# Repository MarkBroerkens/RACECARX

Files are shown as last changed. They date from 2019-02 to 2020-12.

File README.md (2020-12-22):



# RACECAR/X

1:10 autonomous RC robocar that is controlled by NVIDIA AGX Xavier.
Please find furher documentation on the [RACECARX website](https://markbroerkens.github.io/RACECARX/docs/)

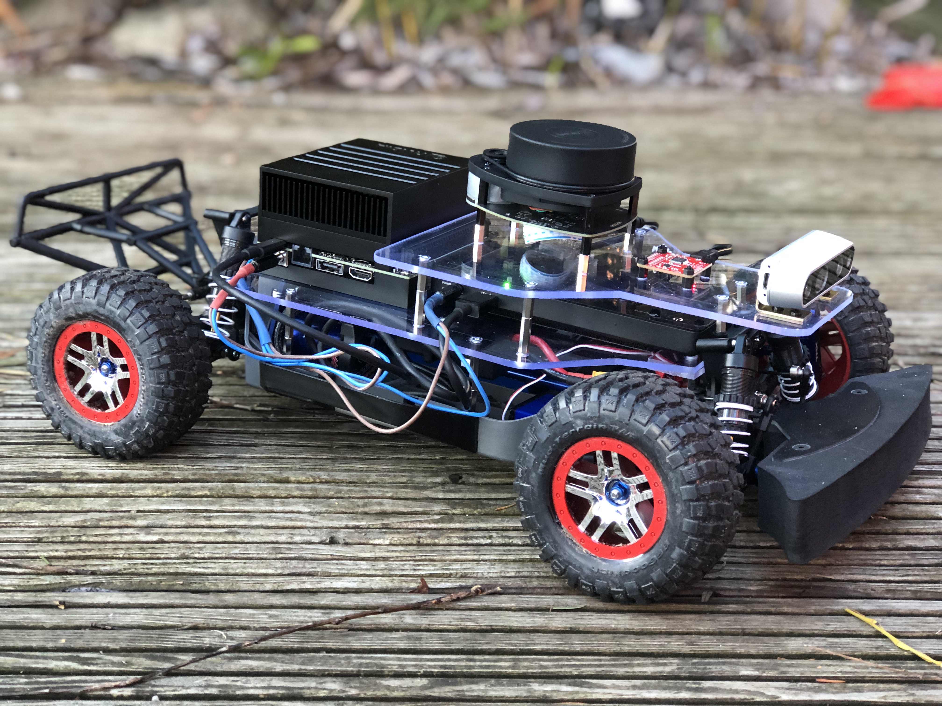
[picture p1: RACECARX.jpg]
RACECAR/X


## Capabilities
* Teleoperation
* Autonomous navigation

## Used technologies
* Docker
* ROS Melodic
* NVidia Xavier
* VESC speed controller
* Intel realsense d435i depth camera
* RPLidar A1 2D laser scanner
* IMU

## Structure of this repository

* [docs](docs) source of the website [RACECARX website](https://markbroerkens.github.io/RACECARX/).
* [hardware](hardware) hardware related resources such as laser cutter descriptions of the platforms
* [software](software) scripts for setting up the software on the Nvidia Jetson and on the PC host 

## Contribution Guide
You are very welcome to contribute to the project. E.g. by 

* reporting an issue via the [github issue](https://github.com/MarkBroerkens/RACECARX/issues) tracker 
* creating a [pull](https://github.com/MarkBroerkens/RACECARX/pulls) request. 

The [Udacity Git Commit Message Style Guide](http://udacity.github.io/git-styleguide/) apply.

The [github workflow](.github/workflows/deploy_website.yml) automatically builds and deploys the website into the [gh-pages](https://github.com/MarkBroerkens/RACECARX/tree/gh-pages) branch. 

You can build the site locally: `bundle exec jekyll build -s docs -d _site`.

## License
The content of this repository is licensed under a [MIT](LICENSE) License

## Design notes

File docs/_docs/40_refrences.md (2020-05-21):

---
permalink: /docs/references/
title: "References"
sidebar:
  nav: "docs"
---

## Similar Projects
RACECAR/X is inspired by the following projects. 

* [MIT RACECAR](https://mit-racecar.github.io/) - MIT RACECAR is an open-source powerful platform for robotics research and education.
* [Jetson racecar](https://www.jetsonhacks.com/category/robotics/jetson-racecar/)
* [F1/10 Autonomous Racing Competition](http://f1tenth.org/) - international community of researchers, engineers, and autonomous systems enthusiasts. It was originally founded at the University of Pennsylvania in 2016 but has since spread to many other institutions worldwide. Great [build](https://f1tenth.org/build.html) instructions and [lectures](https://f1tenth.org/learn.html).
* [OpenZeka Marc](https://github.com/openzeka/marc) - ([translated to english](http://translate.google.com/translate?hl=&sl=tr&tl=en&u=https%3A%2F%2Fopenzeka.com%2Fmarc%2F&sandbox=1))
* [Hypha-ROS racecar](https://hypharosworkshop.wordpress.com/) - Low-cost, high speed (600USD, 3 m/s) 1/10 Autonomous ROS RaceCar (with tutorial for beginner)
* [eagleMK4](https://github.com/r7vme/eagleMK4) - The prototype of autonomous RC car based on MIT Racecar platform
* [Project Omicron](https://project-omicron.github.io/index.html) - build a robot for the Robocup@Work competition
* [JetRacer](https://github.com/NVIDIA-AI-IOT/jetracer) - an autonomous AI racecar using NVIDIA Jetson Nano
* [Multi-agent System for non-Holonomic Racing (MuSHR)](https://mushr.io/) - an open-source robotic hardware and software platform for learning and researching AI in a the setting of autonomous vehicles and mobile robotics.

## Related to Nvidia Jetson

* [Jetson Nano Tools](https://github.com/karaage0703/jetson-nano-tools) - Jetson Nano useful tools (setup, examples)
* [Jetcard install](https://github.com/NVIDIA-AI-IOT/jetcard/blob/master/install.sh) - install script of nvidia jetcard
* [NVIDIA AI IOT](https://github.com/NVIDIA-AI-IOT) - NVIDIA AI IOT Github repositories
* [Isaac SDK](https://docs.nvidia.com/isaac/isaac/doc/index.html) - the main software toolkit for NVIDIA robotics
* [Jetson Community Projects](https://developer.nvidia.com/embedded/community/jetson-projects)
* [Jetson Zoo](https://elinux.org/Jetson_Zoo) - contains instructions for installing various open source add-on packages and frameworks on NVIDIA Jetson, in addition to a collection of DNN models for inferencing.

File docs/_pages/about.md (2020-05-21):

---
permalink: /about/
title: "About"
author_profile: true
---

This project is higly inspired by the [MIT racecar](https://mit-racecar.github.io/) and [Jetson racecar](https://www.jetsonhacks.com/category/robotics/jetson-racecar/).

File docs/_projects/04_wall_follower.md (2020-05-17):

---
permalink: /projects/wall_follower
title: "Wall Follower"
excerpt: Wall follower based on lidar data.
toc: false
classes: wide
---

{% include video id="c6wClUE2E_Q" provider="youtube" %}

{% include video id="4Rs8uSq79dI" provider="youtube" %}

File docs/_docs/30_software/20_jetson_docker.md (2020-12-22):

---
permalink: /docs/software/jetson_docker
title: "Software Setup - Docker on Jetson Xavier"
toc: true
---

The docker images are created on top of the l4t-base image from the Nvidia GPU Cloud.

## Get the installation scripts

```bash
echo 'export RACECARX=$HOME/racecarx' >> ~/.bashrc
echo 'export RACECARX_JETSON=$RACECARX/git/RACECARX/software/jetson' >> ~/.bashrc
source ~/.bashrc
```

```bash
mkdir -p $RACECARX/git
cd $RACECARX/git
git clone https://github.com/MarkBroerkens/RACECARX.git
```

## Install Udev Rules for the Peripherals 
(TODO: should go to pheripherals)

* Alias the Sparkfun 9DoF as /dev/imu
* Alias for electronic speed controller as /dev/vesc
* Alias for the rplidar as /dev/rplidar
* ALias for Intel RealSense D435i camera

```bash
cd $RACECARX_JETSON
./scripts/jetsonInstallUdev.sh
```

make sure we have write access to the VESC and IMU devices

```bash
sudo adduser $USER dialout
```

Further references:

* [ROS and Udev Rules](https://www.clearpathrobotics.com/assets/guides/kinetic/ros/Udev%20Rules.html)

## Build docker container
```bash
cd $RACECARX_JETSON
./scripts/docker_build_ros.sh
```

The docker image supports the following features:

1. Nvidia base image: l4t-base (r32.4.3)
2. ROS melodic
3. Realsense camera

## Initial setup
```bash
cd $RACECARX_JETSON
./scripts/docker_build_racecarx.sh
```

# Run the docker container in interactive mode

```bash
cd $RACECARX_JETSON
./scripts/docker_run_racecarx.sh
```

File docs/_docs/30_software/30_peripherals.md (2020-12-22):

---
permalink: /docs/software/peripherals
title: "Software Setup - Sensors and Actuators"
toc: true
---

## Controller Sony DualShock 4 V2
Connect the Controller via bluetooth

```bash
sudo bluetoothctl
```
Enable the agent and set it as default:

```bash
[bluetooth]# agent on
[bluetooth]# default-agent
```

Power on the Bluetooth controller, and set it as discoverable and pairable:

```bash
[bluetooth]# power on
[bluetooth]# discoverable on
[bluetooth]# pairable on
```

Scan for devices:

```bash
[bluetooth]# scan on
```

Put the DualShock 4 into pairing mode by pressing and holding the PlayStation and Share buttons until the light bar starts flashing.

Discover the DualShock 4 MAC address:

```bash
[bluetooth]# devices
```

Pair with the DualShock 4:

```bash
[bluetooth]# pair DC:0C:FF:B2:79:EE
```

Allow the service authorization request:

```bash
[agent]Authorize service service_uuid (yes/no): yes
```

Trust the DualShock 4:

```bash
[bluetooth]# trust DC:0C:FF:B2:79:EE
```

The DualShock 4 is now paired.

Turn the DualShock 4 off when it's no longer in use by pressing and holding the PlayStation button for 10 seconds. Press the PlayStation button to use the DualShock 4 again.

Test the controller

```bash
sudo apt-get install joystick
ls /dev/input 
jstest /dev/input/js0
```

## Realsense d435i camera
Run the racecarx docker container in interactive mode

```bash
~/racecarx/RACECARX/racecarx.sh
```

Run the firmware update tool and print the connected devices

```bash
rs-fw-update -l
```

My oputput looks like this

```
connected devices:
1) Name: Intel RealSense D435I, serial number: xxxxxxxxx, update serial number: xxxxxxxx, firmware version: 05.11.06.250, USB type: 3.2
```

Find the latest firmware and copy its link 
[latest firmware](https://downloadcenter.intel.com/download/29255/Latest-Firmware-for-Intel-RealSense-D400-Product-Family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)

download and install latest firmware. See also [here](https://dev.intelrealsense.com/docs/firmware-update-tool)

```bash
cd /tmp
wget https://downloadmirror.intel.com/29703/eng/D400_Series_Development_FW_5_12_6_0.zip
apt update # gets the index
apt-get install unzip # installs unzip
unzip D400_Series_Development_FW_5_12_6_0.zip
rs-fw-update -f Signed_Image_UVC_5_12_6_0.bin
```

we should see the updated firmware version

```bash
rs-fw-update -l
```

After the update my output looks like this:
```
connected devices:
1) Name: Intel RealSense D435I, serial number: xxxxxxxxx, update serial number: xxxxxxxx, firmware version: 05.12.06.00, USB type: 3.2
```

## Focbox Electronic Speed Control
* Get the [VESC Tool](https://vesc-project.com/vesc_tool). The free version is sufficient. 
* The required Firmware [VESC_servoout.bin](https://github.com/vedderb/vesc_tool/blob/master/res/firmwares/410_o_411_o_412/VESC_servoout.bin) is available in the [vedderb/vesc_tool](https://github.com/vedderb/vesc_tool) github repository at [res/firmwares/410_o_411_o_412](https://github.com/vedderb/vesc_tool/blob/master/res/firmwares/410_o_411_o_412/)

## SparkFun 9DoF Razor IMU M0
Install Arduino Firmware as described [here](https://github.com/MarkBroerkens/razor_imu_9dof)

## RPLidar A1M8
Installation consists of proper configuration of UDEV rules.

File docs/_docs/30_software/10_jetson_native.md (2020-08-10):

---
permalink: /docs/software/jetson_native
title: "Software Setup - Jetson Xavier"
toc: true
---

## Install JetPack 4.4
* Download and install [NVIDIA SDK Manager](https://developer.nvidia.com/embedded/jetpack)
* Note: Select the manual installation mode. 
  Automatic mode might have issues when starting up in headless mode. See bug 200525134 in the [L4T Release Notes](https://docs.nvidia.com/jetson/l4t/pdf/Jetson_Linux_Driver_Package_Release_Notes_R32.3.1_GA.pdf)
* Notes
 * During first boot I configured _racecarx_ as hostname and 
 * added a user called _mark_ 
  
## Enable password-less login via ssh
In order to be able to login via ssh into the racecarx without typing your password, you can create a pair of private / public ssh keys and upload the public key in the ~/.ssh/autorized_keys on the racecarx.

Create the ssh keys

```bash
ssh-keygen
```

upload the public key to racecarx

```bash
ssh-copy-id mark@racecarx
```

Now you schould be able to login without password by typing

```bash
ssh mark@racecarx
```

## Extend disk memory
### Install M.2 NVMe SSD
JetsonHacks provides a good description for [installing the SSD on the NVIDIA Jetson AGX Xavier](https://www.jetsonhacks.com/2018/10/18/install-nvme-ssd-on-nvidia-jetson-agx-developer-kit/).

### Mount SSD
We mount the partition on the SSD via UUID in order to be robust with respect to potentially changing device identifiers. Especially important if you are using USB devices.

```bash
# create the mount point
sudo mkdir /XavierSSD500

# find UUID of an ext4 partition on SSD. 
# you can search for the label. E.g. label="XavierSSD500"
sudo blkid

# backup the original fstab file that
sudo cp /etc/fstab /etc/fstab.orig

# add mount information to ssd partition into fstab
sudo vim /etc/fstab

# :i (switch to insert mode)
# insert UUID=<yout uuid is identified above>  /XavierSSD500 ext4 nosuid,nodev,auto,nouser 0 2
# <ESC>
# :wq (write and quit)

# mount the ssd according to new data in fstab
sudo mount /XavierSSD500
```

### Move /home to SSD
```bash
# create the new home folder on the SSD
sudo mkdir /XavierSSD500/home
# copy the home folder to the ssd preserving symlinks, permissions, access rights, ...
sudo rsync -aXS /home/. /XavierSSD500/home/.
sudo mv /home /home.orig; sudo ln -s /XavierSSD500/home /home
sudo diff -qr /home /home.orig # diff quietly and move into subfolders

```

Reboot. If everything works:

```bash
sudo rm -rf /home.orig
```

### Move docker data directory to SSD
* Stop the docker daemon

```
sudo service docker stop
```

* Edit configuration file /etc/docker/daemon.json to tell the docker daemon the location of the data directory. Additionally, we anable access to the CUDA compiler (nvcc) during docker build operations by adding "default-runtime": "nvidia":

The content should look like:

```json
{
    "runtimes": {
        "nvidia": {
            "path": "nvidia-container-runtime",
            "runtimeArgs": []
        }
    },
    "default-runtime": "nvidia",
    "graph": "/XavierSSD500/var/lib/docker"
}
```

* Copy the current data directory to the new one

```bash
sudo rsync -aP /var/lib/docker/ /XavierSSD500/var/lib/docker
```

* Rename the old docker directory

```bash
sudo mv /var/lib/docker /var/lib/docker.old
```

This is just a sanity check to see that everything is ok and docker daemon will effectively use the new location for its data.

* Restart the docker daemon

```bash
sudo service docker start
```

* Test

```bash
sudo docker run hello-world
```
This should download and run the hello-world container. Docker should have created several files in /XavierSSD500/var/lib/docker

If everything worked as expected you can delete the old docker folder /var/lib/docker.old. This is only required in case docker was used before and the folder existed.

## Add Wifi / Bluetooth
### Install Wifi/Bluetooth M.2 module
TODO: HW installation of intel 8265 M.2 module

### Enable wifi
JetPack 4.4 should detect the intel 8265 M.2 wifi module out of the box. 
You should see the device wlan0 in the Network Manager:

```bash
nmcli device
```

Create a new wlan connection for you ssid.

```bash
sudo nmcli connection add ifname wlan0 type wifi ssid "B3 5GHz"
```

Configure the authentication mode to WPA and set the password.

```bash
sudo nmcli connection edit wifi-wlan0
```

configure 

```

===| nmcli interactive connection editor |===

Editing existing '802-11-wireless' connection: 'wifi-wlan0'

Type 'help' or '?' for available commands.
Type 'describe [<setting>.<prop>]' for detailed property description.

You may edit the following settings: connection, 802-11-wireless (wifi), 802-11-wireless-security (wifi-sec), 802-1x, ipv4, ipv6, tc, proxy
nmcli> goto wifi
You may edit the following properties: ssid, mode, band, channel, bssid, rate, tx-power, mac-address, cloned-mac-address, generate-mac-address-mask, mac-address-blacklist, mtu, seen-bssids, hidden, powersave, mac-address-randomization
nmcli 802-11-wireless> set mode infrastructure
nmcli 802-11-wireless> back
nmcli> goto wifi-sec
You may edit the following properties: key-mgmt, wep-tx-keyidx, auth-alg, proto, pairwise, group, pmf, leap-username, wep-key0, wep-key1, wep-key2, wep-key3, wep-key-flags, wep-key-type, psk, psk-flags, leap-password, leap-password-flags, wps-method
nmcli 802-11-wireless-security> set key-mgmt wpa-psk
nmcli 802-11-wireless-security> set psk myPasswordGoesHere
nmcli 802-11-wireless-security> save
Connection 'wifi-wlan0' (f425bcdd-c8a5-48b5-906e-b0b002e8aaaa) successfully updated.
nmcli 802-11-wireless-security> quit

```

## Enable bluetooth 
Check if the 8265 wifi / bluetooth module is detected

```bash
lspci
```

```bash
rfkill list
```

Check if bluetooth devices are blocked

```
mark@racecarx:~$ rfkill list
0: bluedroid_pm: Bluetooth
	Soft blocked: no
	Hard blocked: no
1: phy0: Wireless LAN
	Soft blocked: no
	Hard blocked: no
2: hci0: Bluetooth
	Soft blocked: no
	Hard blocked: no
```

if they are soft blocked, then execute

```bash
sudo rfkill unblock bluetooth
```

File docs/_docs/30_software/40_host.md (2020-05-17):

---
permalink: /docs/software/host
title: "Software Setup - Host PC"
toc: true
---

## MacOSX
in order to flash the latest jetpack in the jetson device, you need a Linux machine with Ubuntu 18.04. Note: The Nvidia installer has many dependencies and might lead to some issues after installation. I recommend to install it into a clean Virtual Machine.

* Prepare Virtual Machine with Ubuntu 18.04.
* Install Nvidia [Jetson SDK](https://developer.nvidia.com/embedded/jetpack) Manager

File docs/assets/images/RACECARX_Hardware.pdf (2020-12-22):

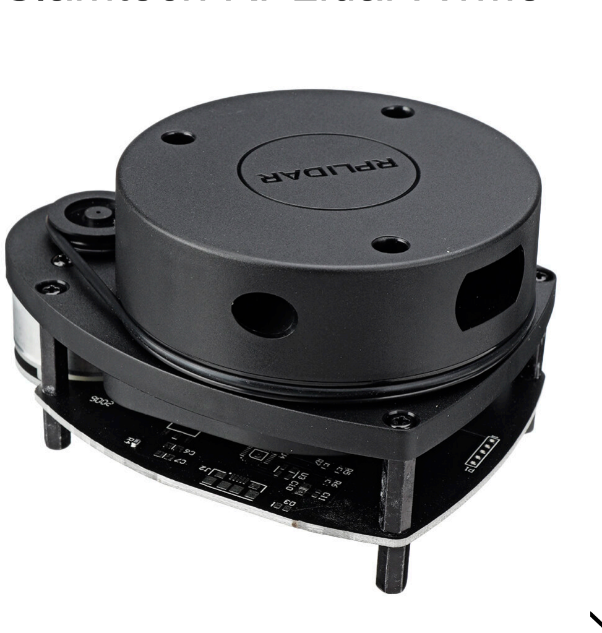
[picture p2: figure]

IMU
SparkFun SEN-14001
9DoF Razor IMU M0

LIDAR
Slamtech RPLidar A1M8

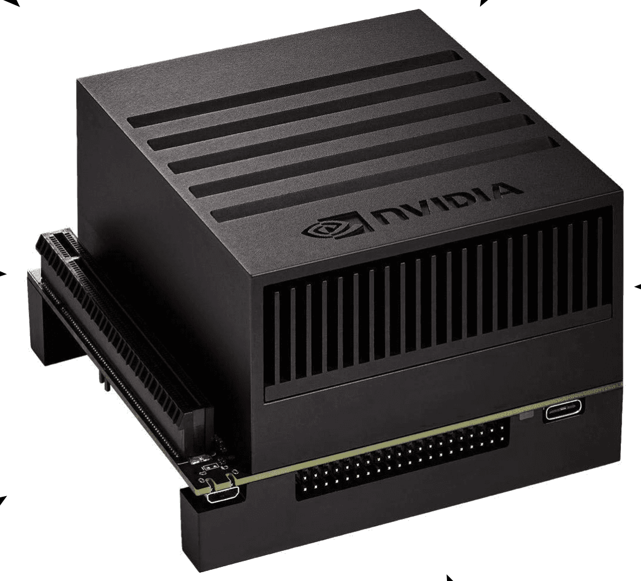
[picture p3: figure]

(Depth) Camera
Intel Realsense d435i

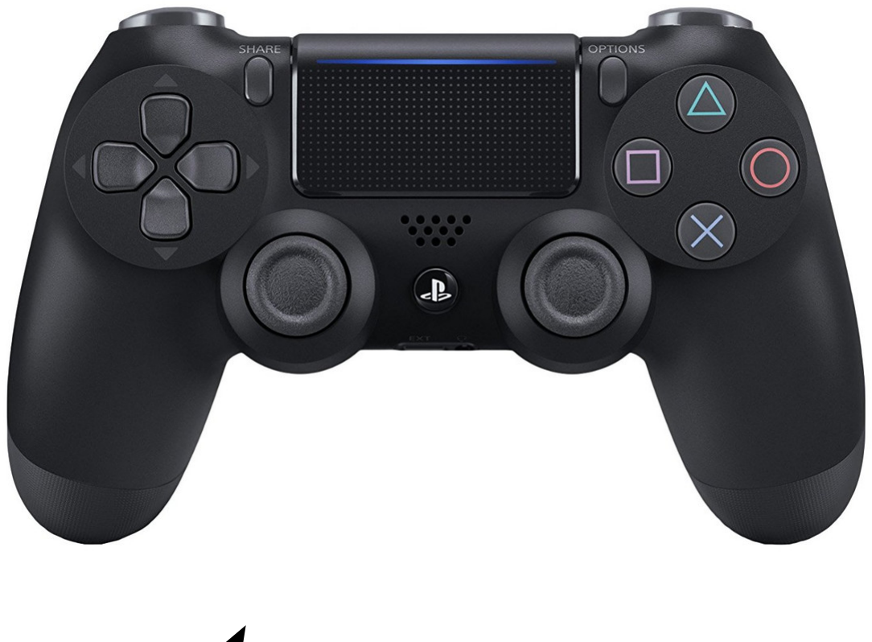
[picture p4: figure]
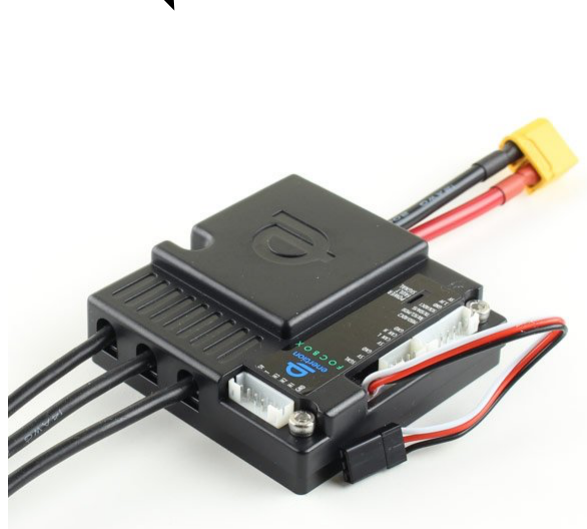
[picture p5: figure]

Electronic Speed Control, Steering, Odometry Focbox VESC 4.12

Teleoperation Controller
Sony PS 4 Controller

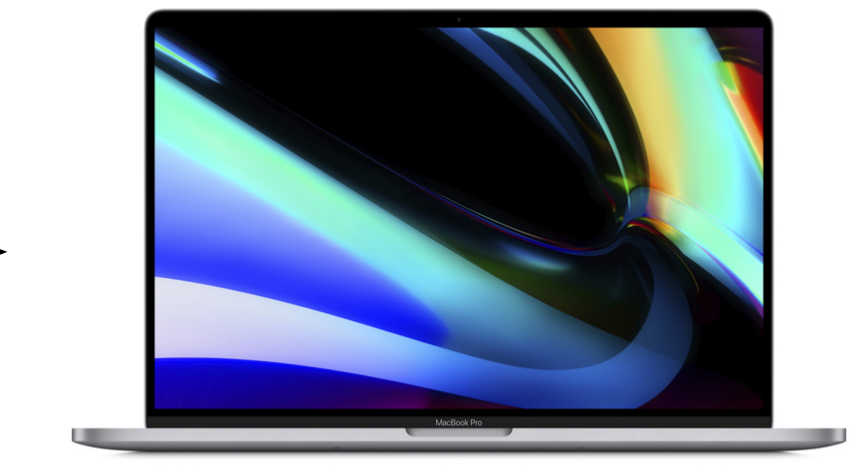
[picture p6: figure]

PC
Mac Book Pro

Bluetooth
USB 2.0

USB 3.0

USB 2.0

WIFI

USB 2.0

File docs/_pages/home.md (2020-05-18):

---
layout: splash
permalink: /
hidden: true
header:
  overlay_color: "#5e616c"
  overlay_image: /assets/images/RACECARX.jpg
excerpt: >
  1:10 Autonomous Racecar based on Nvidia Xavier.
feature_row:
  - image_path: /assets/images/ros_logo_feature.jpg
    alt: "ROS"
    title: "ROS"
    excerpt: "RACECAR/X allows you to build advanced robot software quickly by harnessing the many tools and libraries built into ROS."
    url: "/docs/"
    btn_class: "btn--primary"
    btn_label: "Learn more"
  - image_path: /assets/images/tips_and_tricks_feature.jpg
    alt: "Tipps and Tricks"
    title: "Tipps and Tricks"
    excerpt: "Tipps and tricks for setting up the hardware and software platform."
    url: "/docs/software/jetson_native"
    btn_class: "btn--primary"
    btn_label: "Learn more"
  - image_path: /assets/images/docker_tf_feature.png
    alt: "Tensorflow and Docker"
    title: "Tensorflow and Docker"
    excerpt: "Uses Tensorflow with Docker on the Nvidia Xavier."
    url: "/docs/software/jetson_docker"
    btn_class: "btn--primary"
    btn_label: "Learn more"      
---

{% include feature_row %}

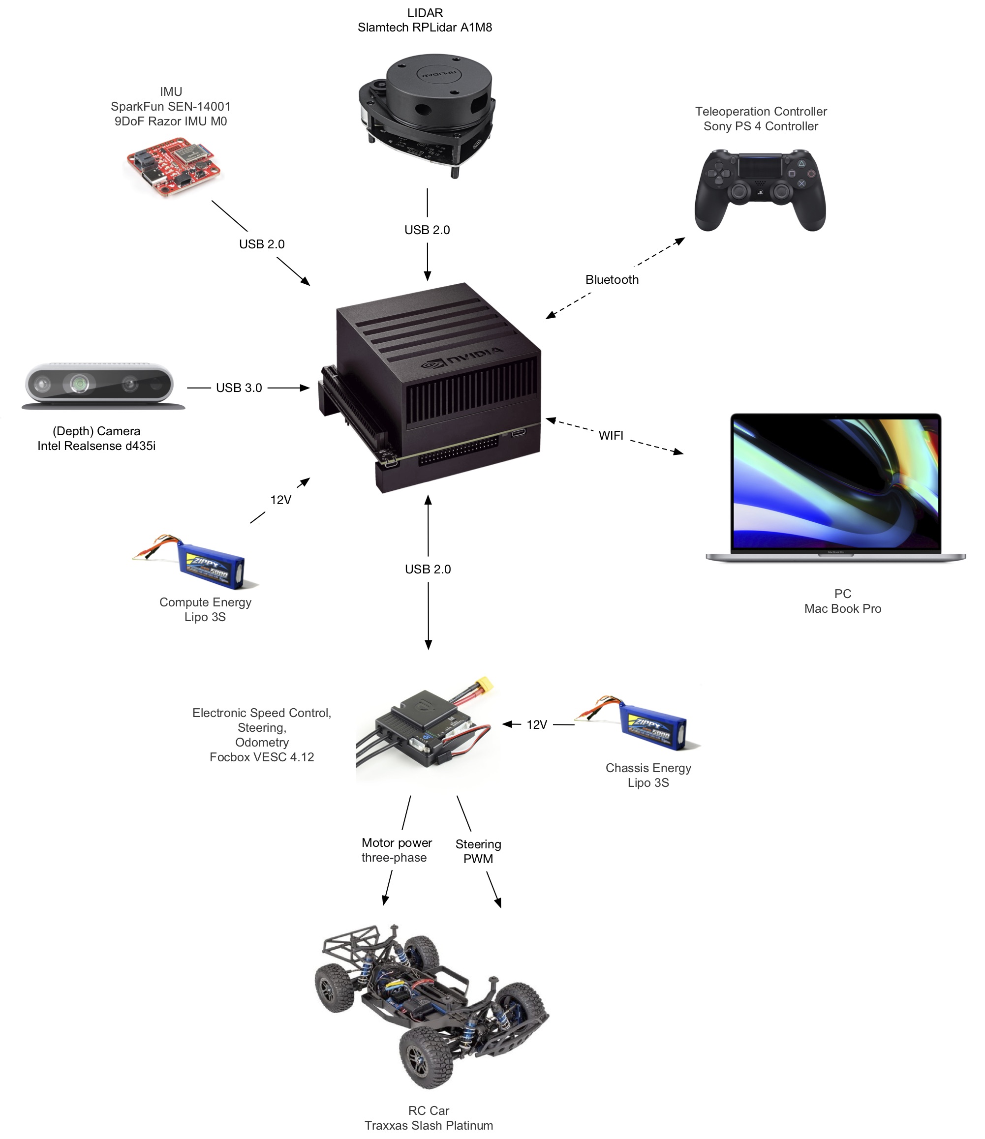
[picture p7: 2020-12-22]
docs/assets/images/RACECARX_Hardware.jpg

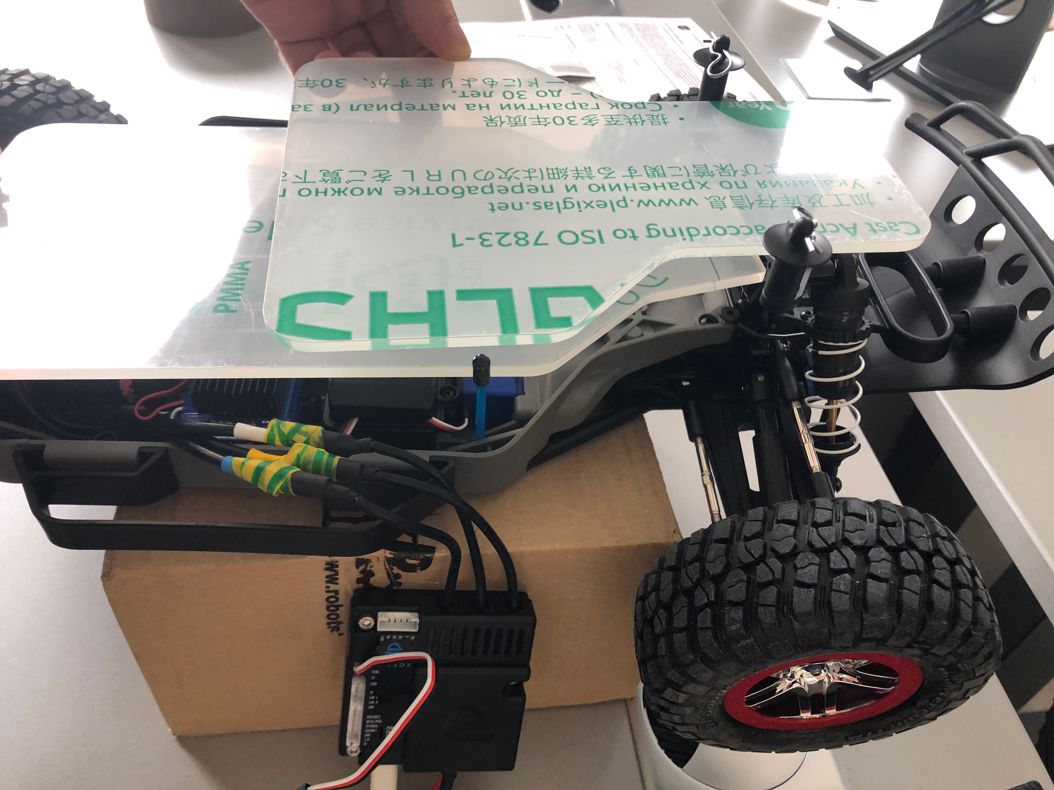
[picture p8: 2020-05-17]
docs/assets/images/tips_and_tricks_feature.jpg

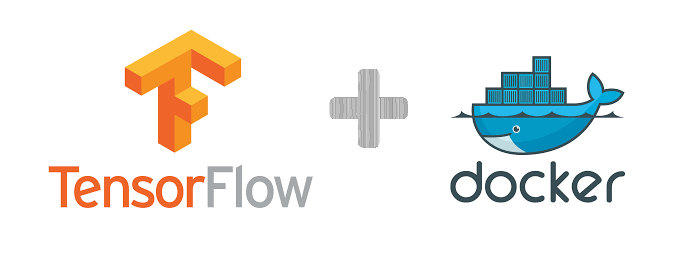
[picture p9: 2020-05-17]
docs/assets/images/docker_tf_feature.png

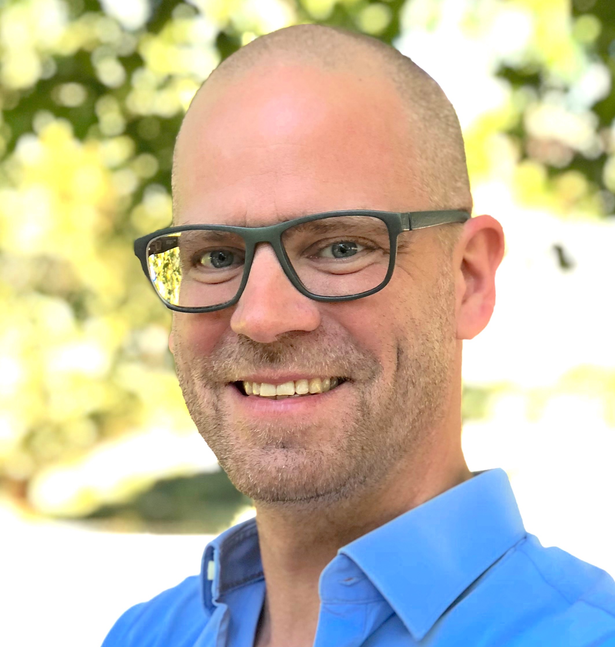
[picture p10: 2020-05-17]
docs/assets/images/bio-photo.jpg

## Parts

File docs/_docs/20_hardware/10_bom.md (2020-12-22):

---
permalink: /docs/hardware/bom
title: "Bill of Materials"
classes: wide
---

price ~3000€

| Component | Where to buy | Specifications | Comments |
| --- | --- | --- | --- |
| 1:10 Race Car chassis | [TRAXXAS Slash 4x4 Platinum](http://mobil.rc-race-shop.de/item/5452583638303452) (499,95€ ) | [TRAXXAS Slash 4x4 Platinum, Model 6804R](https://traxxas.com/products/models/electric/6804Rslash4x4platinum?t=support) | only chassis and brushless motor are used.|
| Front Bumper | [JConcepts 2173 - Traxxas Slash 4X4 - Speed Run Front Bumper Conversion Kit](https://www.rc-race-shop.de/jconcepts/2173-slash-4x4-vorderer-rammer-umruestsatz) (29,95€) | | |
| 2 x LiPo battery 3S | [ZIPPY Flightmax 5000mAh 3S1P 20C](https://hobbyking.com/de_de/zippy-flightmax-5000mah-3s1p-20c.html) (2 x 23,28 €  ) | [ZIPPY Flightmax 5000mAh 3S1P 20C](https://hobbyking.com/de_de/zippy-flightmax-5000mah-3s1p-20c.html) | One for car, one for Jetson |
| 2 x LiPo voltage checker | [lipo voltage checker](https://hobbyking.com/de_de/hobbykingtm-lipo-voltage-checker-2s-8s.html) (2 x 1,86€)| |
| Compute module  | [Nvidia Jetson AGX Xavier Development Kit](https://developer.nvidia.com/embedded/buy/jetson-xavier-devkit) (1349,00€ ) | [User Guide](https://developer.download.nvidia.com/assets/embedded/secure/jetson/xavier/docs/jetson_agx_xavier_developer_kit_user_guide.pdf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) [Nvidia Forum](https://devtalk.nvidia.com/default/topic/1039020/jetson-agx-xavier/links-to-jetson-xavier-resources-amp-wiki/) [Documentation](https://developer.nvidia.com/embedded/downloads#?search=Jetson%20AGX%20Xavier) [FAQ](https://developer.nvidia.com/embedded/faq#xavier-faq) [Technical Blog](https://devblogs.nvidia.com/nvidia-jetson-agx-xavier-32-teraops-ai-robotics/?ncid=so-fac-mdjngxxrmllhml-69163)| register for the Nvidia developmenter program for special discount. |
| ESC | [Enertion FOCBOX](https://electricboardsolutions.com/products/enertion-focbox) (159,00€) | [VESC Project](https://vesc-project.com/documentation) | alternative: [Turnigy SK8-ESC V4.12](https://hobbyking.com/de_de/turnigy-sk8-esc-v4-12-for-electric-skateboard-conversion-w-bec.html)|
| Battery adapter | [HXT 4mm bis XT-60 Batterie-Adapter](https://hobbyking.com/de_de/hxt-4mm-to-xt-60-battery-adapter-2pcs-bag.html) (3,60€) | | required to connect FOCBOX with Zippy Lipo |
| M.2 SSD | [Samsung 970 EVO 500GB, M2 2280](https://www.amazon.de/dp/B07CGGP7SV/ref=pe_3044161_189395811_TE_SCE_dp_1) (134,86€) | [Samsung 970 EVO NVMe M.2 SSD, 500GB](https://www.samsung.com/de/memory-storage/970-evo-nvme-m-2-ssd/MZ-V7E500BW/) |  M.2 Key M HDD|
| M.2 Wifi | [INTEL Dual Band Wireless-AC 8265 Desktop Kit](https://www.amazon.de/dp/B077HKW5HK/ref=pe_3044161_189395811_TE_SCE_3p_dp_1) (31,17€) | | includes antennas and can run in access point mode |
| 10x USB 3.0 hub | [ORICO 40W 10 Ports USB 3.0 hub](https://www.amazon.de/gp/product/B075QZ88DM) (32,99€) | | |
| usb c to usb b adapter | [USB 3.1 Type C (USB-C) auf Type B (USB-B) Kable](https://www.amazon.de/gp/product/B00UXKTJE0) | | |
| 2D Lidar | [Slamtec RPLidar A1M8](https://www.exp-tech.de/sensoren/entfernungnaeherung/8946/rplidar-a1m8-360-degree-laser-scanner-kit-12m) (99,90€) | [Introduction and Datasheet](http://bucket.download.slamtec.com/e9e096e9d9f30205d665260abe2cfb0c2dd62efa/LD108_SLAMTEC_rplidar_datasheet_A1M8_v1.0_en.pdf) | |
| IMU | [SparkFun MPU-9250 9DoF Razor IMU M0](https://www.mouser.de/new/sparkfun/sparkfun-dev-16832-openlog-artemis/) (34,95€) | [Hookup Guide](https://learn.sparkfun.com/tutorials/9dof-razor-imu-m0-hookup-guide?_ga=1.59377581.1661814591.1474882863) [Datasheet MPU-9250](https://cdn.sparkfun.com/assets/learn_tutorials/5/5/0/MPU9250REV1.0.pdf) [Datasheet SAMD21](https://cdn.sparkfun.com/datasheets/Dev/Arduino/Boards/Atmel-42181-SAM-D21_Datasheet.pdf) | |
| Camera | [Intel realsense D435i](https://click.intel.com/intel-realsense-depth-camera-d435i-imu.html) (~250€)| [Intel Realsense D400 DatSheet](https://www.intel.com/content/dam/support/us/en/documents/emerging-technologies/intel-realsense-technology/Intel-RealSense-D400-Series-Datasheet.pdf)| |
| 2 x Hobby glass | [25cm x 50cm x 4mm](https://www.hornbach.de/shop/Hobbyglas-4x250x500-mm-Glatt-klar/1477845/artikel.html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) (2 x ~6,00€) | | |
| M3 standoffs/nuts/etc. | [M3 Nylon Black Hex Screw Nut Spacer Standoff (260 pieces)](https://www.amazon.de/gp/product/B01MFF5XIC) | | | 
| controller | [PlayStation 4 - DualShock 4 Wireless Controller](https://www.amazon.de/gp/product/B01GVQUX3U) (60,13€) | | |

# Tools
* [iFixit Pro Tech Toolkit](https://www.amazon.de/gp/product/B01GF0KV6G) (59,95€)
* [iFixit Tragbar Elektroschocks Matte](https://www.amazon.de/gp/product/B01BLPBOS4) (29,95€)
* [IMax B6AC V2 Balance Charger](https://www.amazon.de/VINGO®ORIGINAL-Netzteil-Batterie-Balance-Ladegerät/dp/B01AXVI6YW/ref=sr_1_1?ie=UTF8&qid=1540673676&sr=8-1&keywords=IMAX+Balance+Charger) (48,99€)

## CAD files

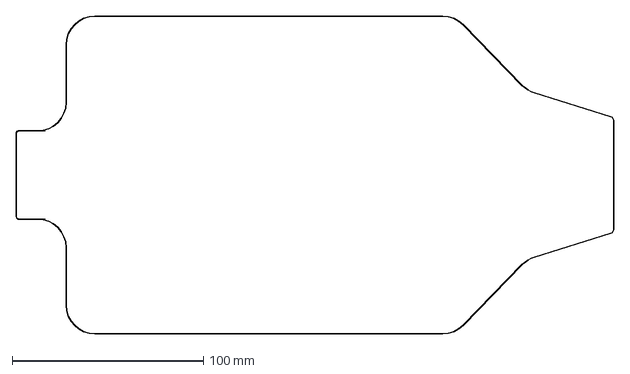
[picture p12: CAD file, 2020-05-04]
hardware/racecarx_lower_platform.dxf
312.0 x 166.0 mm

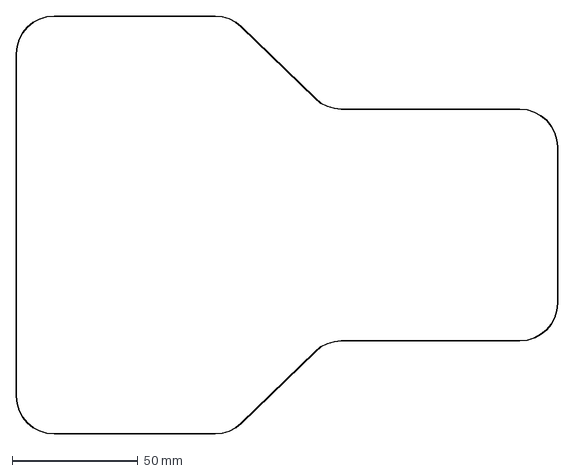
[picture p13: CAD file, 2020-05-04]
hardware/racecarx_upper_platform.dxf
215.0 x 166.0 mm

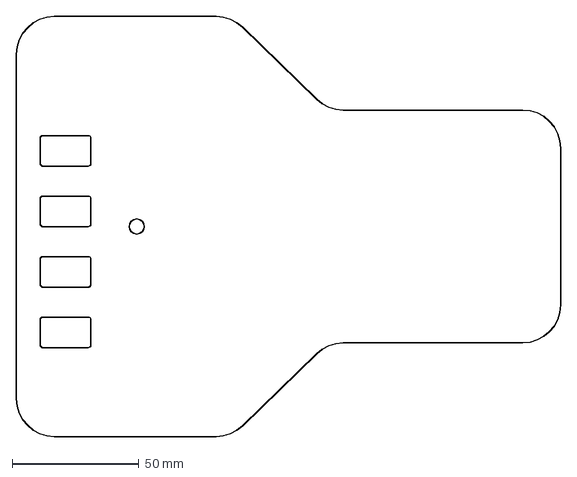
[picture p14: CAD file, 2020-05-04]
hardware/racecarx_upper_platform_for_usb.dxf
215.0 x 166.0 mm

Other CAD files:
hardware/racxecarx_platforms.f3d

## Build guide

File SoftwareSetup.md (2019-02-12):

This tutorial is based on
* JetPack 4.1.1 Developer Preview
* ROS Melodic

# Setting up the hardware components
##  Xavier: update to JetPack 4.1.1 Developer Preview
[Installing JetPack 4.1.1 Developer Preview on Jetsonhacks.com](https://www.jetsonhacks.com/2018/10/05/jetpack-4-1-developer-preview-nvidia-jetson-agx-xavier-developer-kit/)

Note: After installing JetPack, host computer is not able to apt-get update. This happens since the installer adds some ARM repositories. You will have to add [arch=amd64,i386] for each line in /etc/apt/sources.list starting with 'deb '. See [Issue on Nvidia DevTalk](https://devtalk.nvidia.com/default/topic/1004601/jetson-tx2/after-installing-jetpack3-0-host-computer-is-not-able-to-apt-get-update/post/5247401/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)

## M.2 SSD
move home to SSD

## M.2 WIFI
check config

configure as access point

## Controller Sony DualShock 4 V2
The Xavier doesn't come with a Bluetooth controller. You can get the [DualShock 4 USB Wireless Adaptor](https://www.playstation.com/de-de/explore/accessories/dualshock-4-usb-wireless-adaptor/) in order to connect the Dualshock controller.

The pairing is described in the [DUALSHOCK®4 USB Wireless Adaptor Instruction Manual](https://www.playstation.com/en-nz/content/dam/support/manuals/scee/web-manuals/peripherals/ps4/ds4-usb-adapter/DS4_USB_Adapter_Ins_Manual_EN.pdf/)
```bash
sudo apt-get install joystick
ls /dev/input
jstest /dev/input/js0
```

## Focbox Electronic Speed Control
Get the [VESC Tool](https://vesc-project.com/vesc_tool). The free version is sufficient. The required Firmware [VESC_servoout.bin](https://github.com/vedderb/vesc_tool/blob/master/res/firmwares/410_o_411_o_412/VESC_servoout.bin) is available in the [vedderb/vesc_tool](https://github.com/vedderb/vesc_tool) github repository at [res/firmwares/410_o_411_o_412](https://github.com/vedderb/vesc_tool/blob/master/res/firmwares/410_o_411_o_412/)

## SparkFun 9DoF Razor IMU M0

## RPLidar A1M8

## Intel RealSense Depth Camera D435i
get a native Windows 10 installation and follow the [Intel update instructions](https://downloadcenter.intel.com/download/28481/Latest-Firmware-for-Intel-RealSense-D400-Product-Family?v=t)

Note: The Linux updater is made for linux x86 and thus cannot be executed on the Xavier

## Rebuilding the kernel
First of all, you need to download necessary files like shown below to rebuild kernel:
```bash
cd ~/git
git clone https://github.com/MarkBroerkens/RACECARX-buildKernelXavier.git
```

see also: [Intel RealSense D435i on NVIDIA Jetson AGX Xavier](https://www.jetsonhacks.com/2019/01/21/intel-realsense-d435i-on-nvidia-jetson-agx-xavier/)

# Integration
## Install ROS Melodic
The racecar code runs using ROS (Robot Operating System) libraries, more on that later. Now let's install ROS:
(For more detailed instructions on how to install: http://wiki.ros.org/kinetic/Installation/Ubuntu). Or take the short path:

```bash
cd ~/git
git clone https://github.com/MarkBroerkens/RACECARX-installROSXavier.git
```

## Install ROS Nodes for RACECAR/X
```bash
cd ~/git
git clone https://github.com/MarkBroerkens/RACECARX-ROS.git
```

## Autostart ROS at boot
get robot-upstart from source (marks repos)
```bash

```

# References
* [OpenZeka Marc](https://github.com/openzeka/openzeka-marc-doc/edit/master/Documentation.md)
* [MIT RACECAR](https://mit-racecar.github.io)

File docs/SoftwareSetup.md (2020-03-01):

<TITLE>RACECARX Software Setup</TITLE>

[toc]

This tutorial is based on

 * JetPack 4.3
 * ROS Melodic

# Setup NVIDIA Xavier

## Install JetPack 4.3
* Download and install [NVIDIA SDK Manager](https://developer.nvidia.com/embedded/jetpack)
* Note: Select the manual installation mode. 
  Automatic mode might have issues when starting up in headless mode. See bug 200525134 in the [L4T Release Notes](https://docs.nvidia.com/jetson/l4t/pdf/Jetson_Linux_Driver_Package_Release_Notes_R32.3.1_GA.pdf)
* Notes
 * During first boot a configured _racecarx_ as hostname and 
 * added a user called _mark_ 
  
## Enable password-less login via ssh
In order to be able to login via ssh into the racecarx without typing your password, you can create a pair of private / public ssh keys and upload the public key in the ~/.ssh/autorized_keys on the racecarx.

Create the ssh keys

```bash
ssh-keygen
```

upload the public key to racecarx

```bash
ssh-copy-id mark@racecarx
```

Now you schould be able to login without password by typing

```bash
ssh mark@racecarx
```

## Extend disk memory
### Install M.2 NVMe SSD
JetsonHacks provides a good description for [installing the SSD on the NVIDIA Jetson AGX Xavier](https://www.jetsonhacks.com/2018/10/18/install-nvme-ssd-on-nvidia-jetson-agx-developer-kit/).

### Mount SSD
We mount the partition on the SSD via UUID in order to be robust with respect to potentially changing device identifiers. Especially important if you are using USB devices.

```bash
# create the mount point
sudo mkdir /XavierSSD500

# find UUID of an ext4 partition on SSD. 
# you can search for the label. E.g. label="XavierSSD500"
sudo blkid

# backup the original fstab file that
sudo cp /etc/fstab /etc/fstab.orig

# add mount information to ssd partition into fstab
sudo vim /etc/fstab

# :i (switch to insert mode)
# insert UUID=<yout uuid is identified above>  /XavierSSD500 ext4 nosuid,nodev,auto,nouser 0 2
# <ESC>
# :wq (write and quit)

# mount the ssd according to new data in fstab
sudo mount /XavierSSD500
```

### Move /home to SSD
```bash
# create the new home folder on the SSD
sudo mkdir /XavierSSD500/home
# copy the home folder to the ssd preserving symlinks, permissions, access rights, ...
sudo rsync -aXS /home/. /XavierSSD500/home/.
sudo mv /home /home.orig; sudo ln -s /XavierSSD500/home /home
sudo diff -qr /home /home.orig # diff quietly and move into subfolders

```

Reboot. If everything works:

```bash
sudo rm -rf /home.orig
```

### Move docker data directory to SSD
* Stop the docker daemon

```
sudo service docker stop
```

* Edit configuration file /etc/docker/daemon.json to tell the docker daemon what is the location of the data directory. The content should look like:

```json
{
    "runtimes": {
        "nvidia": {
            "path": "nvidia-container-runtime",
            "runtimeArgs": []
        }
    },
    "graph": "/XavierSSD500/var/lib/docker"
}
```

* Copy the current data directory to the new one

```bash
sudo rsync -aP /var/lib/docker/ /XavierSSD500/var/lib/docker
```

* Rename the old docker directory

```bash
sudo mv /var/lib/docker /var/lib/docker.old
```

This is just a sanity check to see that everything is ok and docker daemon will effectively use the new location for its data.

* Restart the docker daemon

```bash
sudo service docker start
```

* Test

```bash
sudo docker run hello-world
```
This should download and run the hello-world container. Docker should have created several files in /XavierSSD500/var/lib/docker

If everything worked as expected you can delete the old docker folder /var/lib/docker.old. This is only required in case docker was used before and the folder existed.

## Add Wifi / Bluetooth
### Install Wifi/Bluetooth M.2 module
TODO: HW installation of intel 8265 M.2 module

### Enable wifi
JetPack 4.3 should detect the intel 8265 M.2 wifi module out of the box. 
You should see the device wlan0 in the Network Manager:

```bash
nmcli device
```

Create a new wlan connection for you ssid.

```bash
sudo nmcli connection add ifname wlan0 type wifi ssid "B3 5GHz"
```

Configure the authentication mode to WPA and set the password.

```bash
sudo nmcli connection edit wifi-wlan0
```

configure 

```

===| nmcli interactive connection editor |===

Editing existing '802-11-wireless' connection: 'wifi-wlan0'

Type 'help' or '?' for available commands.
Type 'describe [<setting>.<prop>]' for detailed property description.

You may edit the following settings: connection, 802-11-wireless (wifi), 802-11-wireless-security (wifi-sec), 802-1x, ipv4, ipv6, tc, proxy
nmcli> goto wifi
You may edit the following properties: ssid, mode, band, channel, bssid, rate, tx-power, mac-address, cloned-mac-address, generate-mac-address-mask, mac-address-blacklist, mtu, seen-bssids, hidden, powersave, mac-address-randomization
nmcli 802-11-wireless> set mode infrastructure
nmcli 802-11-wireless> back
nmcli> goto wifi-sec
You may edit the following properties: key-mgmt, wep-tx-keyidx, auth-alg, proto, pairwise, group, pmf, leap-username, wep-key0, wep-key1, wep-key2, wep-key3, wep-key-flags, wep-key-type, psk, psk-flags, leap-password, leap-password-flags, wps-method
nmcli 802-11-wireless-security> set key-mgmt wpa-psk
nmcli 802-11-wireless-security> set psk myPasswordGoesHere
nmcli 802-11-wireless-security> save
Connection 'wifi-wlan0' (f425bcdd-c8a5-48b5-906e-b0b002e8aaaa) successfully updated.
nmcli 802-11-wireless-security> quit

```

## Enable bluetooth 
Check if the 8265 wifi / bluetooth module is detected

```bash
lspci
```

```bash
rfkill list
```

Check if bluetooth devices are blocked

```
mark@racecarx:~$ rfkill list
0: bluedroid_pm: Bluetooth
	Soft blocked: no
	Hard blocked: no
1: phy0: Wireless LAN
	Soft blocked: no
	Hard blocked: no
2: hci0: Bluetooth
	Soft blocked: no
	Hard blocked: no
```

if they are soft blocked, then execute

```bash
sudo rfkill unblock bluetooth
```

# Setup Racecarx docker
## Build the docker images
### Login to NGC docker registry
The docker images are created on top of the l4t-base image from the Nvidia GPU Cloud.
Before accessing locked NGC content, you must sign up for an NGC account and obtain an API key as explained in the NGC Getting Started Guide. Then log in to the NGC registry from the command line as follows.
Log in to the NGC container registry.
```bash
$ sudo docker login nvcr.io
```
When prompted for your user name, enter the following text:
```bash
$oauthtoken
```

The $oauthtoken username is a special user name that indicates that you will authenticate with an API key and not a username and password.
When prompted for your password, enter your NGC API key as shown in the following example.

```bash
Username: $oauthtoken
Password: yourAuthTokenFromNGC
```

Tip: When you get your API key, copy it to the clipboard so that you can paste the API key into the command shell when you are prompted for your password.

After successful login you will get the following message

```
WARNING! Your password will be stored unencrypted in /home/mark/.docker/config.json.
Configure a credential helper to remove this warning. See
https://docs.docker.com/engine/reference/commandline/login/#credentials-store

Login Succeeded
```

Reference: [Logging in to the NGC container registry](https://docs.nvidia.com/ngc/ngc-user-guide/pullcontainer.html#logging-in-to-ngc-registry)

### Get the installation scripts

````bash
mkdir ~/racecarx
cd ~/racecarx
git clone https://github.com/MarkBroerkens/RACECARX.git
````

### Build docker container
```bash
cd RACECARX/jetson/docker
sudo make build
```

TODO: describe content of racecarx docker image

1. l4t-base
2. ros
3. realsense camera

### Initial setup
```bash
cd ~/racecarx/RACECARX
./installRACECARX_Xavier.sh
```

# Setup sensors and actuators
## Controller Sony DualShock 4 V2
<TODO> how to connect pair controller?

```bash
sudo apt-get install joystick
ls /dev/input
jstest /dev/input/js0
```

## Realsense d435i camera
Run the racecarx docker container in interactive mode

```bash
~/racecarx/RACECARX/racecarx.sh
```

Run the firmware update tool and print the connected devices

```bash
rs-fw-update -l
```

My oputput looks like this

```
connected devices:
1) Name: Intel RealSense D435I, serial number: xxxxxxxxx, update serial number: xxxxxxxx, firmware version: 05.11.06.250, USB type: 3.2
```

Find the latest firmware and copy its link 
[latest firmware](https://downloadcenter.intel.com/download/29255/Latest-Firmware-for-Intel-RealSense-D400-Product-Family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)

download and install latest firmware. See also [here](https://dev.intelrealsense.com/docs/firmware-update-tool)

```bash
cd /tmp
wget https://downloadmirror.intel.com/29255/eng/D400_Series_Development_FW_5_12_1.zip
apt update # gets the index
apt-get install unzip # installs unzip
unzip D400_Series_Development_FW_5_12_1.zip
rs-fw-update -f Signed_Image_UVC_5_12_1_0.bin
```

we should see the updated firmware version

```bash
rs-fw-update -l
```

## Wide angle camera
### 

## Focbox Electronic Speed Control
Get the [VESC Tool](https://vesc-project.com/vesc_tool). The free version is sufficient. The required Firmware [VESC_servoout.bin](https://github.com/vedderb/vesc_tool/blob/master/res/firmwares/410_o_411_o_412/VESC_servoout.bin) is available in the [vedderb/vesc_tool](https://github.com/vedderb/vesc_tool) github repository at [res/firmwares/410_o_411_o_412](https://github.com/vedderb/vesc_tool/blob/master/res/firmwares/410_o_411_o_412/)

## SparkFun 9DoF Razor IMU M0

## RPLidar A1M8

## Intel RealSense Depth Camera D435i
get a native Windows 10 installation and follow the [Intel update instructions](https://downloadcenter.intel.com/download/28481/Latest-Firmware-for-Intel-RealSense-D400-Product-Family?v=t)

Note: The Linux updater is made for linux x86 and thus cannot be executed on the Xavier

# Install Racecarx

# Setting up the hardware components

# Integration
## Install ROS Melodic
The racecar code runs using ROS (Robot Operating System) libraries, more on that later. Now let's install ROS:
(For more detailed instructions on how to install: http://wiki.ros.org/kinetic/Installation/Ubuntu). Or take the short path:

```bash
cd ~/git
git clone https://github.com/MarkBroerkens/RACECARX-installROSXavier.git
```

## Install ROS Nodes for RACECAR/X
```bash
cd ~/git
git clone https://github.com/MarkBroerkens/RACECARX-ROS.git
```

## Autostart ROS at boot
get robot-upstart from source (marks repos)

```bash

```

# References
* [OpenZeka Marc](https://github.com/openzeka/openzeka-marc-doc/edit/master/Documentation.md)
* [MIT RACECAR](https://mit-racecar.github.io)

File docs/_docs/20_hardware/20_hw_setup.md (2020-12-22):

---
permalink: /docs/hardware/architecture
title: "Hardware Components"
classes: wide
---

{% include figure image_path="/assets/images/RACECARX_Hardware.jpg"  caption="RACECAR/X Hardware Components" %}

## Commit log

2019-02-12 Add files via upload
    added current image of the racecarx
2019-12-09 added udev rules for realsense camera and rplidar
2020-03-01 improved of lowlevel driver installation when using docker
2020-05-04 Added drawings of upper and lower platform that have been used for laser cutting
    [racecarx_lower_platform.dxf, racecarx_upper_platform.dxf, racecarx_upper_platform_for_usb.dxf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]
2020-08-10 updated docker file according to jetpack 4.4 credits to https://github.com/dusty-nv/jetson-containers
2020-08-11 fix: added missing eigen and yaml libs
    * libeigen3-dev - required by vesc
    * libyaml-cpp-dev - required by muxer
2020-12-22 docs: aligned bill of materials with current hardware configuration
    removed no longer used parts such as openMV cam and bluetooth dongle
2020-12-22 docs: added lipo batteries to hardware archtecture
